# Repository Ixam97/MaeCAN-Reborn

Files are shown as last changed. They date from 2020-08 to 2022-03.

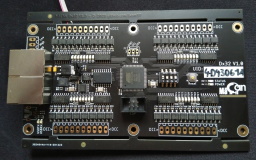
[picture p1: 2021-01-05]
MaeCAN_Dx32/img/Dx32_2_prev.jpg

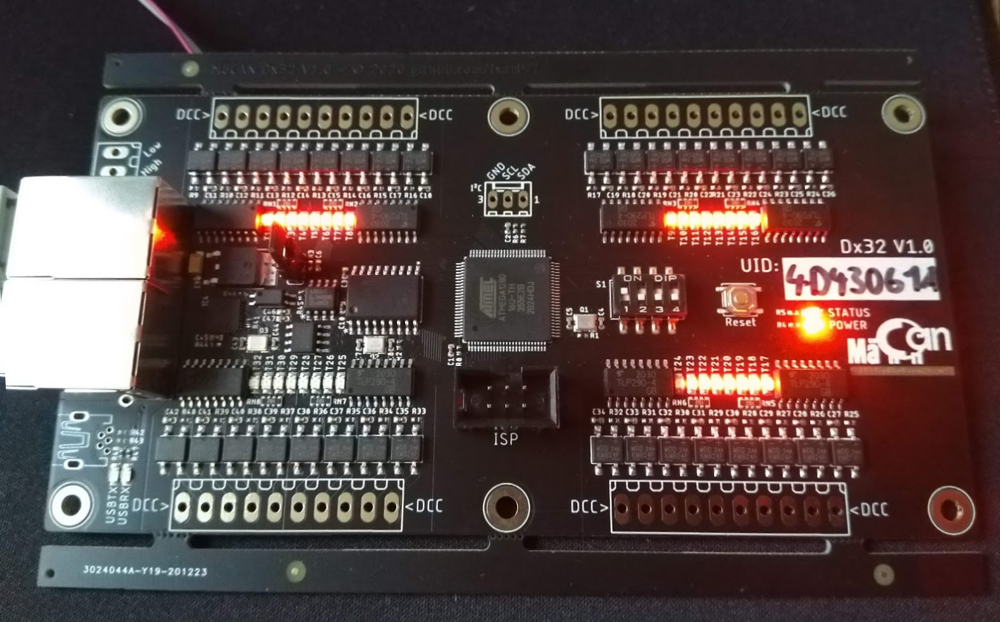
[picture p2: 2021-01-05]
MaeCAN_Dx32/img/Dx32_3.jpg

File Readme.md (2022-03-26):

# <b>MäCAN _Reborn_ </b>

Die zweite Generaton der MäCAN-Komponenten für den [Märklin CAN-Bus][candoku]

- <b>[MäCAN _Bootloader_][bootloader]</b><br>
    
- <b>[MäCAN _MP5x16_][mp5x16]</b><br>
    
    
- <b>[MäCAN _Dx32_][dx32]</b><br>
    
    
## Changelog

### [2022-03-26.1]
#### Hinzugefügt:
 - MP5x8+S: Kombination aus Signal- und Weichendecoder zum testen, kompatibel mit der MP5x16-Platine.
#### Änderungen:
 - MP5+D | Rückmeldefehler behoben, Einstellungen für die Schaltzeit und -verzögerung.
 - MP5x16 | Rückmeldefehler behoben.
 - Bootloader | Unterstützt nun 16-Bit Page-Addresse (Rückwärtskomatibel mit alten Updatern).
 - Bootloader | Nach einem fehlerhaften oder abgebrochenen Update wird der Programmspeicher gelöscht. Das Gerät verbleibt im Booloader, bis ein Update erfolgreich abgeschlossen wurde.
 - Allgemein | Der CAN-Ringpuffer blockiert nicht mehr, wenn er voll läuft.

### [2021-09-14.1]
#### Hinzugefügt:
- Allgemein | Source und Binarys für den maecan-updater für SRSEII und Windows.
- Bootloader | Unterstützung für NScale Grundmodule.
- MP5+D | Abwandlung des MP5x16 für die alternative Nutzung einiger Ports.
#### Änderungen:
- MP5x16 | Korrekte Abhandlung von Config-Kanal-Abfragen durch ein Userinterface.
- Bootloader | UID-Vergleich korrigiert.
### [2021-03-13.2]
#### Hinzugefügt:
- Allgemein | Fehlermeldung hinzugefügt, falls MCAN mit einem nicht unterstützten Controller verwendet wird.

### [2021-03-13.1]
#### Änderungen:
- Allgemein | Die Dokumentation in mcan.h wurde umfangreich erweitert.
- Allgemein | Die Berechnung des Hash wird durch mcan_init() übernommen. Die vorgefertigten send-Funktionen benötigen keine UID und keinen Hash mehr als Parameter. Dx32 und MP5x16 wurden entsprechend angepasst.
- Allgemein compareUID() ist jetzt Teil von MCAN.

### [2021-03-12.1]
#### Änderungen:
- Allgemein | MCAN beinhaltet nun mcp2515_basic und wurde aufgeräumt, um die Nutzung zu vereinfachen. Eine nutzung in Arduino-Sketches ist möglich.

#### Hinzugefügt:
- Dx32 | Version 1.0, Konfiguration und EEPROM-Nutzung wurde vollständig integriert. 
- Dx32 | Der DIP-Schalter stellt folgende Funktionen bereit: 1: Bootloader-Modus (noch nicht im Bootloader integriert), 2: New Line bei SLCAN zum Debugging, 3: Silent-Mode reagiert nicht auf Ping-Anfragen

### [2021-01-27.1]
#### Hinzugefügt:
- Allgemein | In mcp2515_basic ist nun SLCAN integriert. Ist das Symbol "SLCAN" definiert wird die serielle Schnittstelle als CAN-Interface genutzt. Standard sind 500000 Baud. Hierfür wurde die Interruptbehandlung in mcp2515_basic integriert. Nach `init_mcp2515()` kann mit `readCanFrame()` ausgewertet werden. SLCAN und der physische CAN werden gleichwertig behandelt. Im selben Zuge wurde für CAN-Frames ein Ring-Buffer implementiert. SLCAN ist auch im Bootloader verfügbar.

#### Änderungen:
- MP5x16 | Die Ansteuerung der Status-LED wurde an Dx32 angeglichen.

### [2021-01-25.1]
#### Hinzugefügt:
- Allgemein | Neue Funktion "sendStatus" in der mcan-Bibliothek zum senden von Statuskanalwerten.
- Dx32 | Konfigurationskanal-Werte können abgefragt werden.

### [2021-01-24.1]
#### Änderungen:
- Allgemein | Ein Fehler in der Übertragung von Konfigurationskanälen in der mcan.c wurde behoben.
- Dx32 | Basisfunktionalität wurde hergestellt (Belegterkennung mit Timeout und Gleisspannungserkennung).

### [2021-01-05.1]
#### Änderungen:
- Allgemein | Die Firmware aller Koponenten sowie des Bootloaders wurden in einer Atmel Studio-Solution zusammen geführt, um auf gemeinsame Dateien zugreifen zu können.
- Allgemein | Vereinheitlichung von Ordner- und Dateinamen ohne Umlaute.
- Allgemein | Nicht benötigte defines in mcan.h entfernt und für den ATmega1280 hinzugefügt.
- MP5x16 | Die Heartbeat-LED hat einen Fade-Effekt erhalten.
- Bootloader | Unterstützung für den Dx32 mit ATmega1280.
- Dx32 | Leitungsbenennung für zwei Rückmelde-LEDs an die Portbenennung angepasst.

#### Hinzugefügt:
- Dx32 | Erste Testsoftware mit einem Lauflicht und Helligkeitssteuerung für die Rückmelde-LEDs.

### [2020-12-26.2]
#### Änderungen:
- Bootloader + MP5x16 | Anpassung an die Compiler-Flags für die CPU-Frequenz, da Delays nicht richtig funktioniert haben.
- MP5x16 | Kleinere Änderungen, mit denen bisherige Compiler-Warnungen behandelt wurden.

### [2020-12-26.1]
#### Änderungen:
- Dx32 | Fehlerhafte Anbindung der externen Taktquelle für die USB-Schnittstelle korrigiert (Hardware V1.1).
- Bootloader | Makefile hinzugefügt, mit der der Bootloader Außerhalb von Atmel Studio für eines oder alle Boards kompilliert werden kann (Software V1.2).
- Bootloader | main.c durch maecan-bootloader.c ersetzt.

#### Hinzugefügt:
- Bootloader | Vorkompillierte Hex-Dateien für Busankoppler und MP5x16 hinzugefügt.

### [2020-12-22.1]
#### Änderungen:
- MP5x16 | Möglichkeit einer einstellbaren ID über den DIP-Schalter für eine einfachere Adressierung.

#### Hinzugefügt
- Dx32 | Erster Upload der Hardware.

### [2020-08-27.2]
#### Änderungen:
- Readme-Dateien angepasst

### [2020-08-27.1]
#### Hinzugefügt:
- MP5x16 | Erster Upload
- Bootloader |  Erster Upload

[candoku]: https://www.maerklin.de/fileadmin/media/service/software-updates/cs2CAN-Protokoll-2_0.pdf
[bootloader]: Bootloader
[mp5x16]: MäCAN_MP5x16
[dx32]: MäCAN_Dx32

[//]: # (Orange: #FE7D37, Blau: #007EC6)

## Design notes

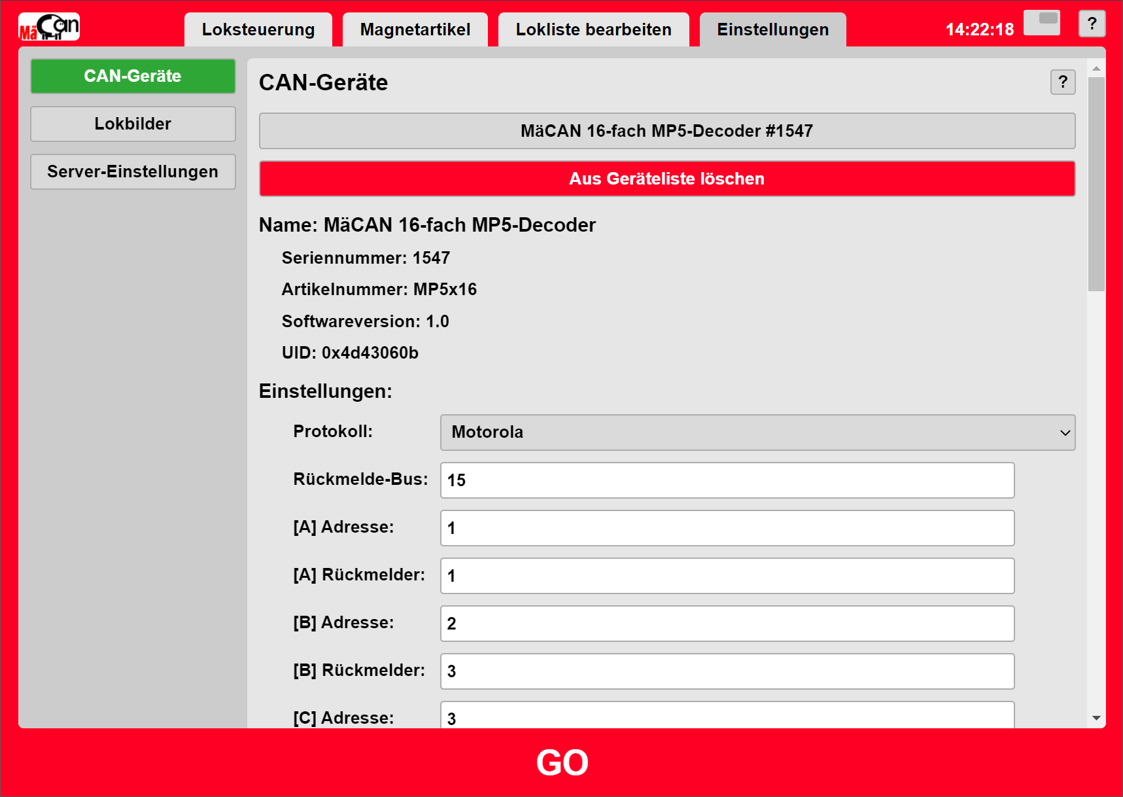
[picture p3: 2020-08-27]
MaeCAN_MP5x16/img/MP5x16_ui_1.png

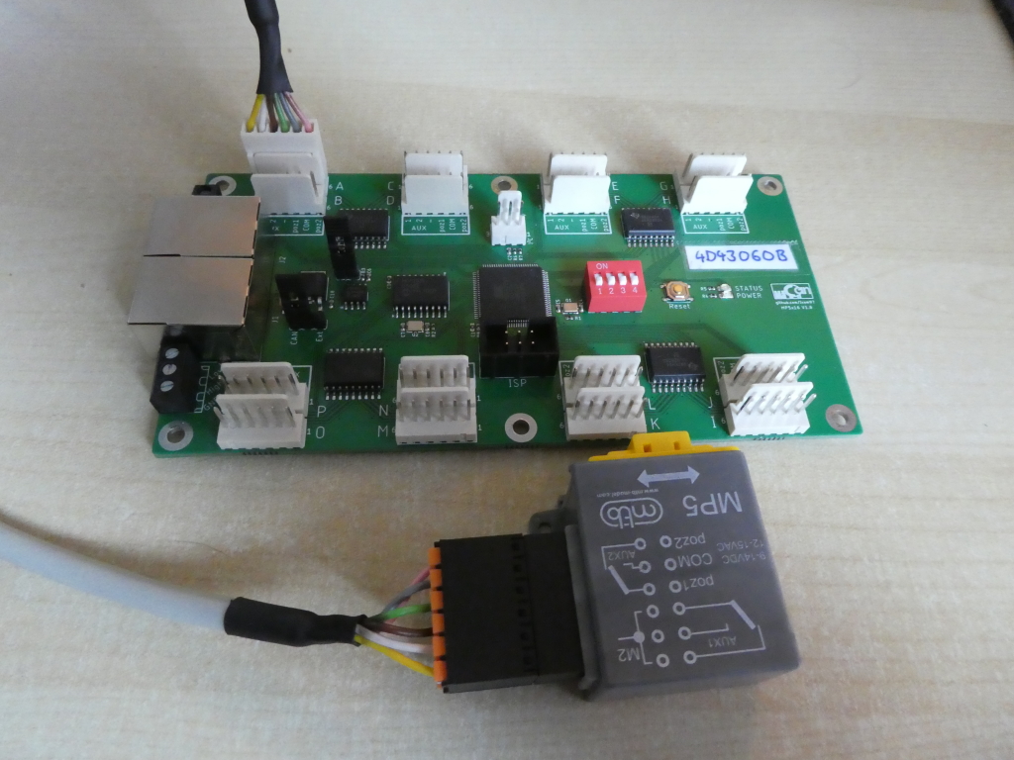
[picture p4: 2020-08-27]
MaeCAN_MP5x16/img/MP5x16_2.jpg

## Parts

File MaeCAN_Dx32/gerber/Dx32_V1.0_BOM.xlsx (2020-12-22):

Qty | Designator | Footprint | Comment | LCSC Part #
8 | RN1, RN2, RN3, RN4, RN5, RN6, RN7, RN8 | 0603_x4 | 1k | C20197
1 | C9 | CASE-A_3216 | 10u | C7171
39 | C1, C2, C3, C6, C10, C11, C12, C13, C14, C15, C16, C17, C18, C19, C20, C21, C22, C23, C24, C25, C26, C27, C28, C29, C30, C31, C32, C33, C34, C35, C36, C37, C38, C39, C40, C41, C42, C46, C47 | C0402 | 100n | C1525
5 | R6, R7, R8, R44, R45 | R0402 | 10k | C25744
1 | R3 | R0402 | 120 | C25079
3 | Q1, Q2, Q3 | 3.2X2.5_KX-7 | 16MHZ | C13738
3 | R1, R2, R41 | R0402 | 1M | C26083
4 | R4, R5, R47, R48 | R0402 | 1k | C11702
1 | C45 | C0402 | 1u | C52923
2 | R42, R43 | R0402 | 22 | C25092
6 | C4, C5, C7, C8, C43, C44 | C0402 | 22p | C1555
32 | R9, R10, R11, R12, R13, R14, R15, R16, R17, R18, R19, R20, R21, R22, R23, R24, R25, R26, R27, R28, R29, R30, R31, R32, R33, R34, R35, R36, R37, R38, R39, R40 | R0402 | 33 | C25105
1 | R46 | R0402 | 330 | C25104
1 | IC5 | SOIC-8_3.9x4.9x1.27P | ADUM1201ARZ-RL7 | C9669
1 | IC4 | QFN-32_EP_5.0x5.0x0.5P | ATMEGA16U2 | C17317
1 | IC1 | QFP-100_14.0x14.0x0.5P | ATMEGA2560 | C22460
1 | RESET | SMD-SW-4 | TS-1187A-B-A-B | C318884
32 | B1, B2, B3, B4, B5, B6, B7, B8, B9, B10, B11, B12, B13, B14, B15, B16, B17, B18, B19, B20, B21, B22, B23, B24, B25, B26, B27, B28, B29, B30, B31, B32 | MBF_3.8x4.7x2.5P | KMB24F | C113927
1 | IC8 | TO-252-2 | L78M05 | C58069
1 | IC3 | SOIC-18 | MCP2515-I/SO | C12368
1 | IC2 | SOIC-8 | TJA1050 | C6952
1 | S1 | SW-SMD-8_6.2x11.1x2.54P | DMR-04-V-T/R | C225009
1 | OK9 | SOP-4_2.7x4.4x1.27P | TLP290 | C73839
8 | OK1, OK2, OK3, OK4, OK5, OK6, OK7, OK8 | SOIC-16_4.4x10.3x1.27P | TLP290-4 | C39031
3 | STATUS, USBRX, USBTX | LED_0805 | yellow | C2296
33 | POWER, T1, T2, T3, T4, T5, T6, T7, T8, T9, T10, T11, T12, T13, T14, T15, T16, T17, T18, T19, T20, T21, T22, T23, T24, T25, T26, T27, T28, T29, T30, T31, T32 | LED_0805 | red | C84256

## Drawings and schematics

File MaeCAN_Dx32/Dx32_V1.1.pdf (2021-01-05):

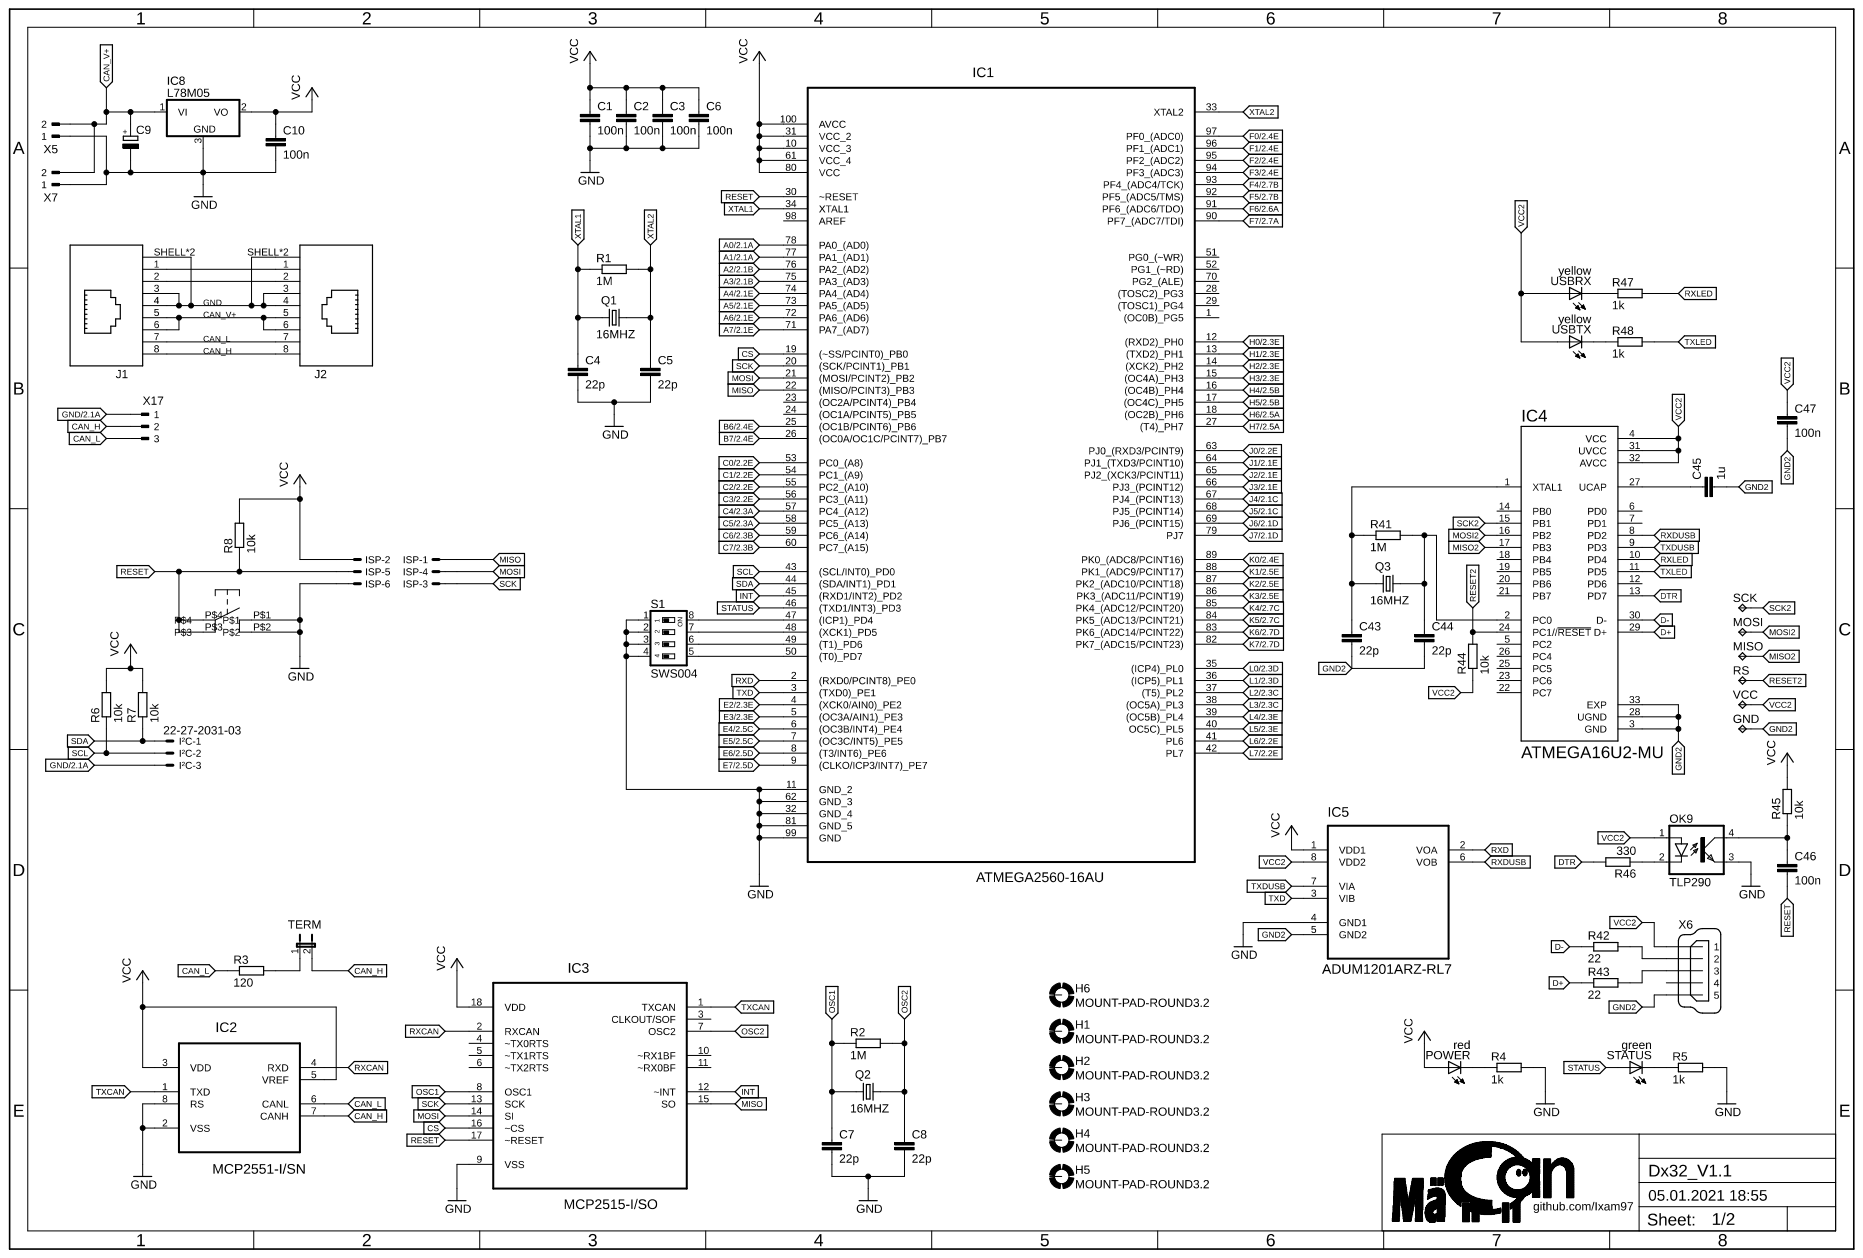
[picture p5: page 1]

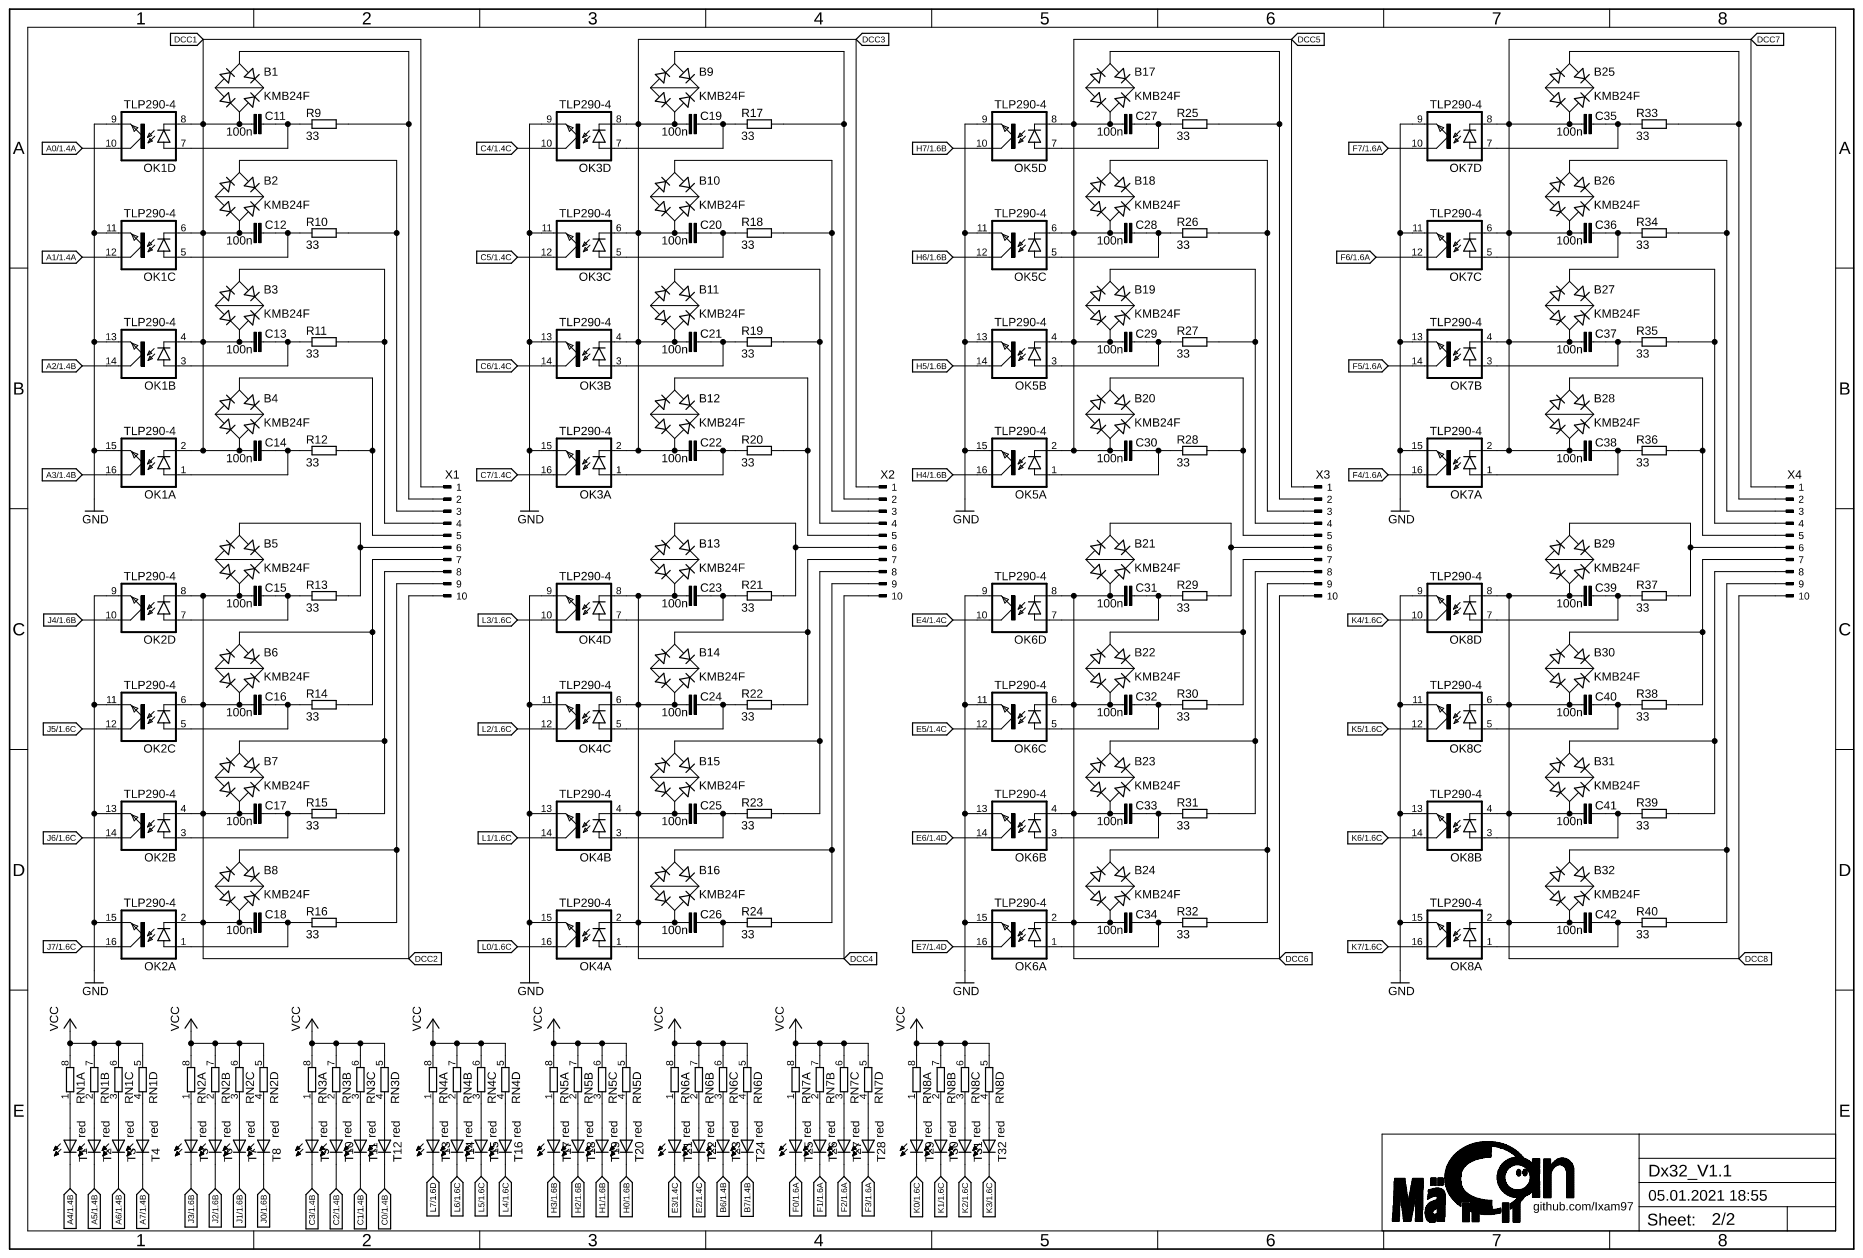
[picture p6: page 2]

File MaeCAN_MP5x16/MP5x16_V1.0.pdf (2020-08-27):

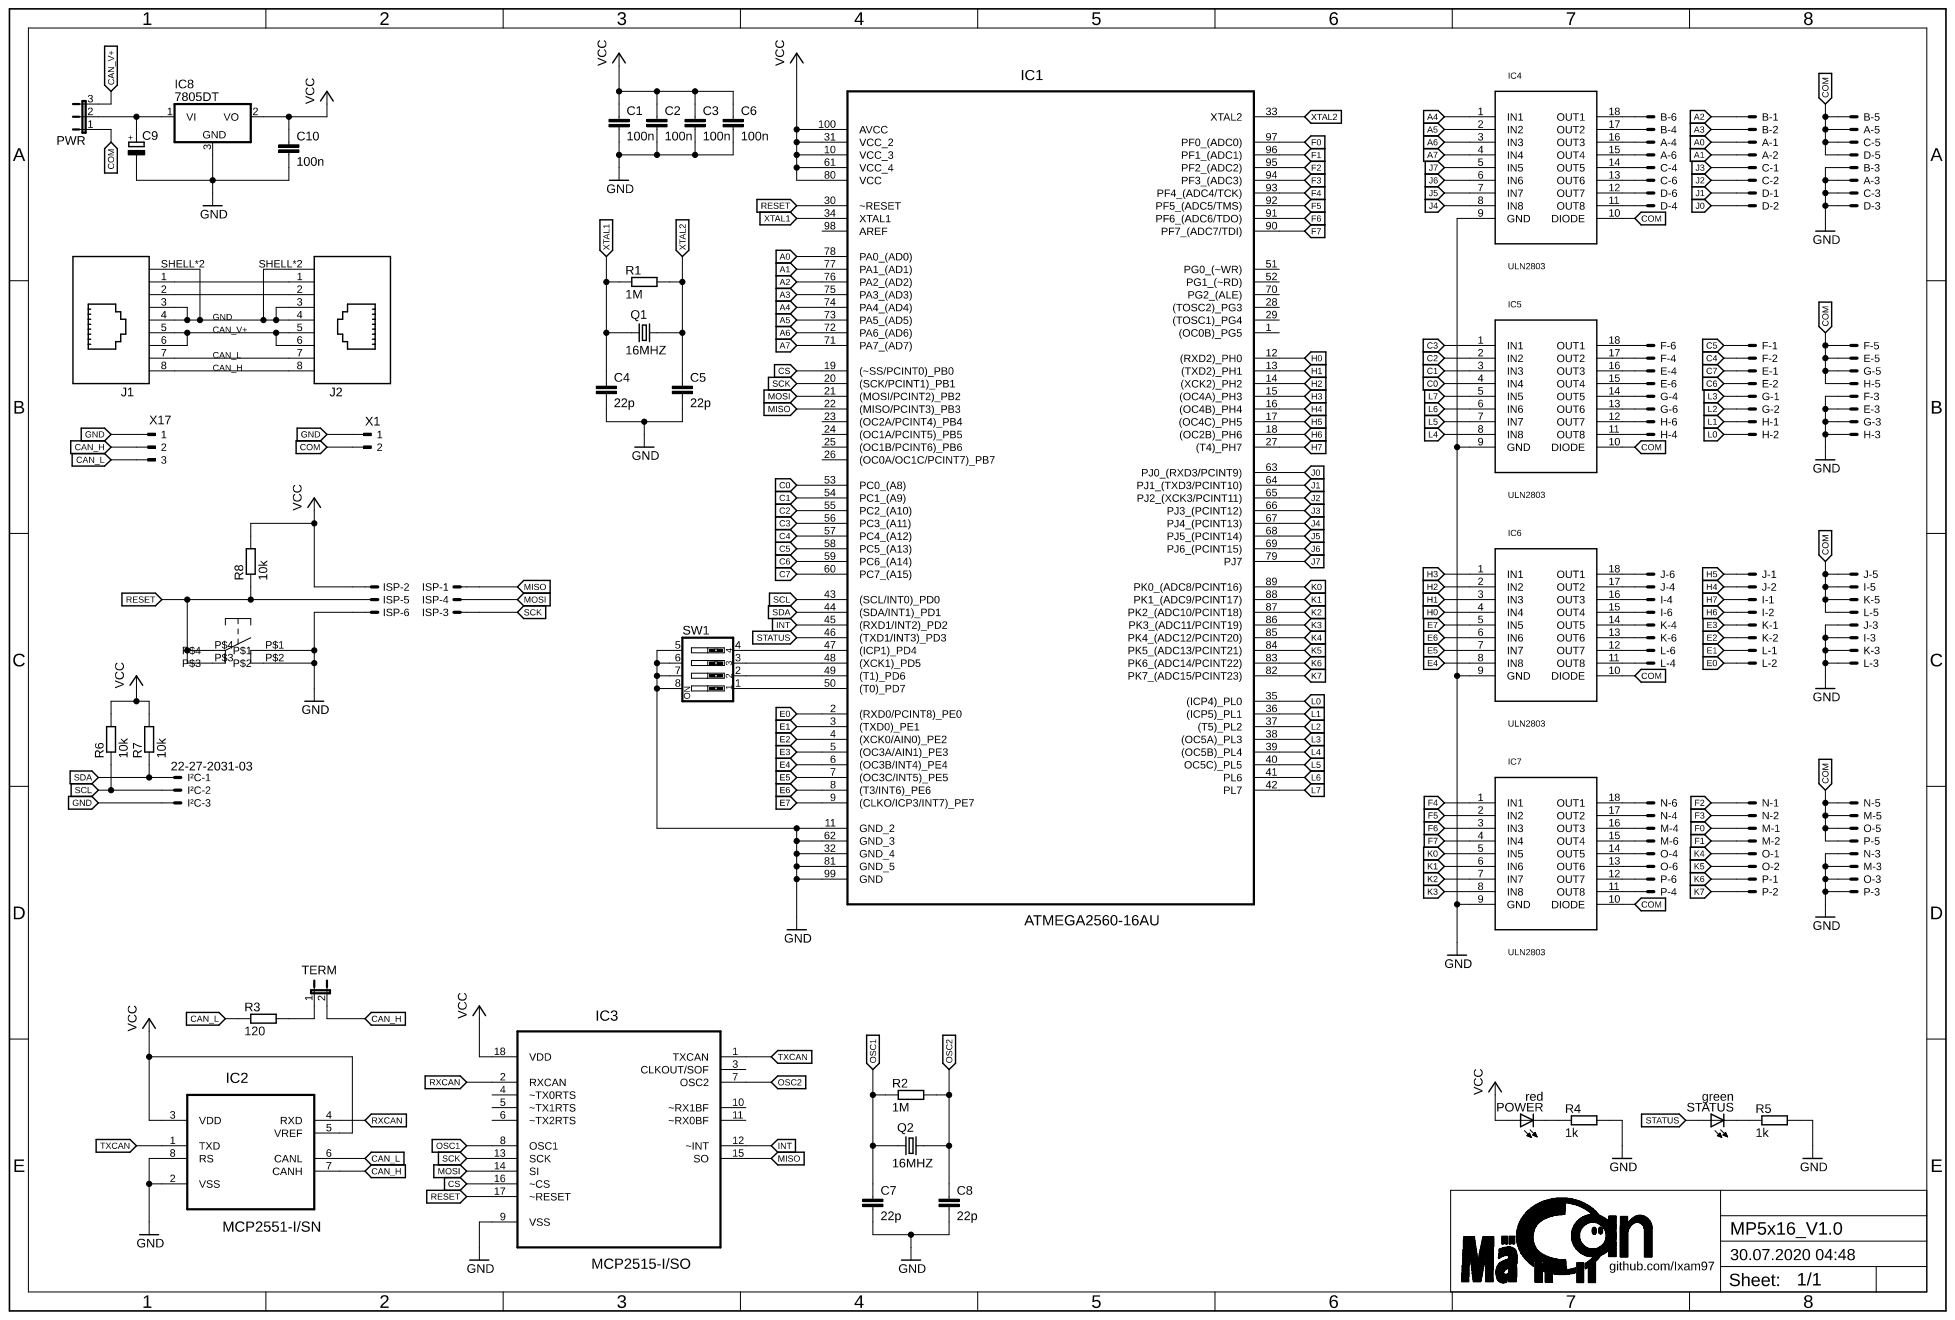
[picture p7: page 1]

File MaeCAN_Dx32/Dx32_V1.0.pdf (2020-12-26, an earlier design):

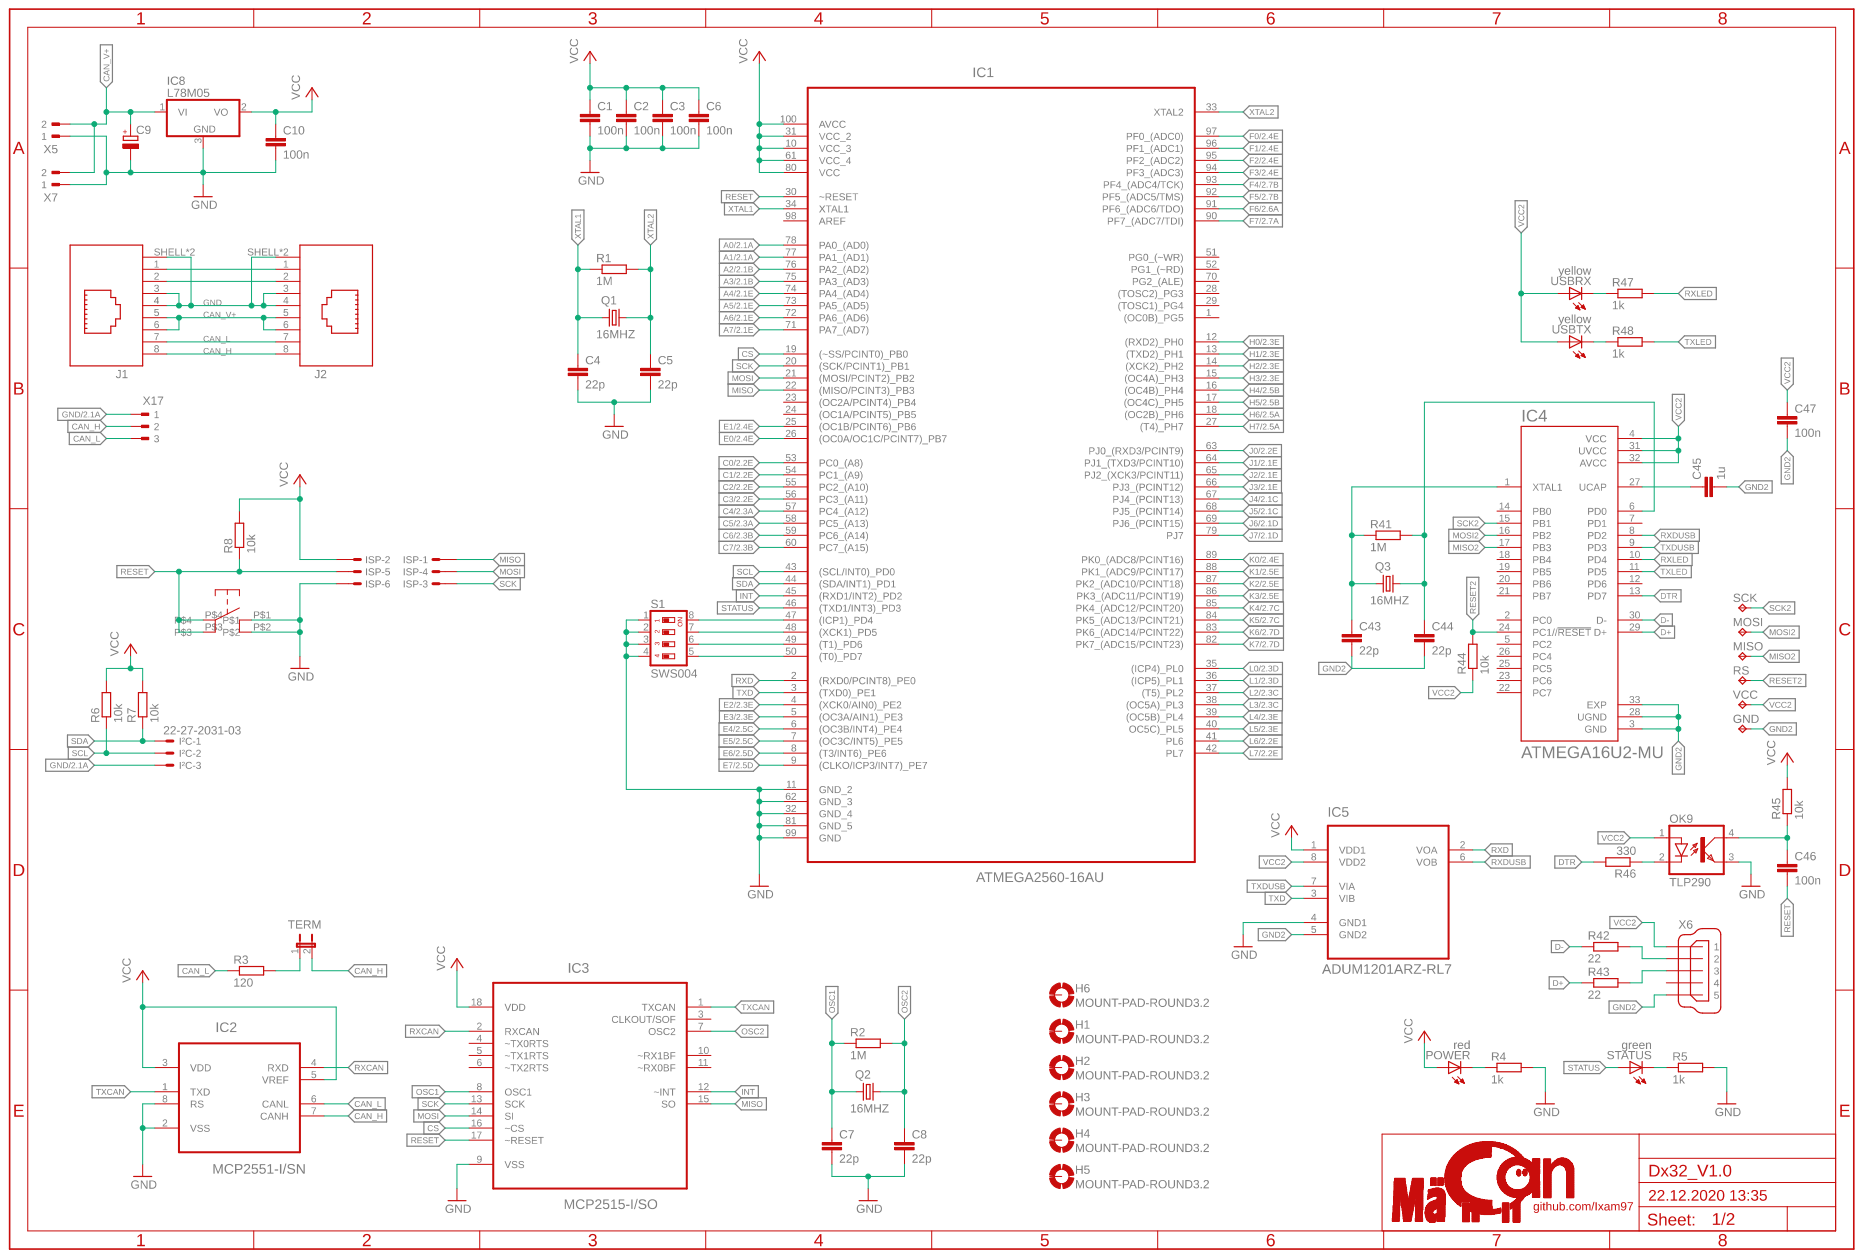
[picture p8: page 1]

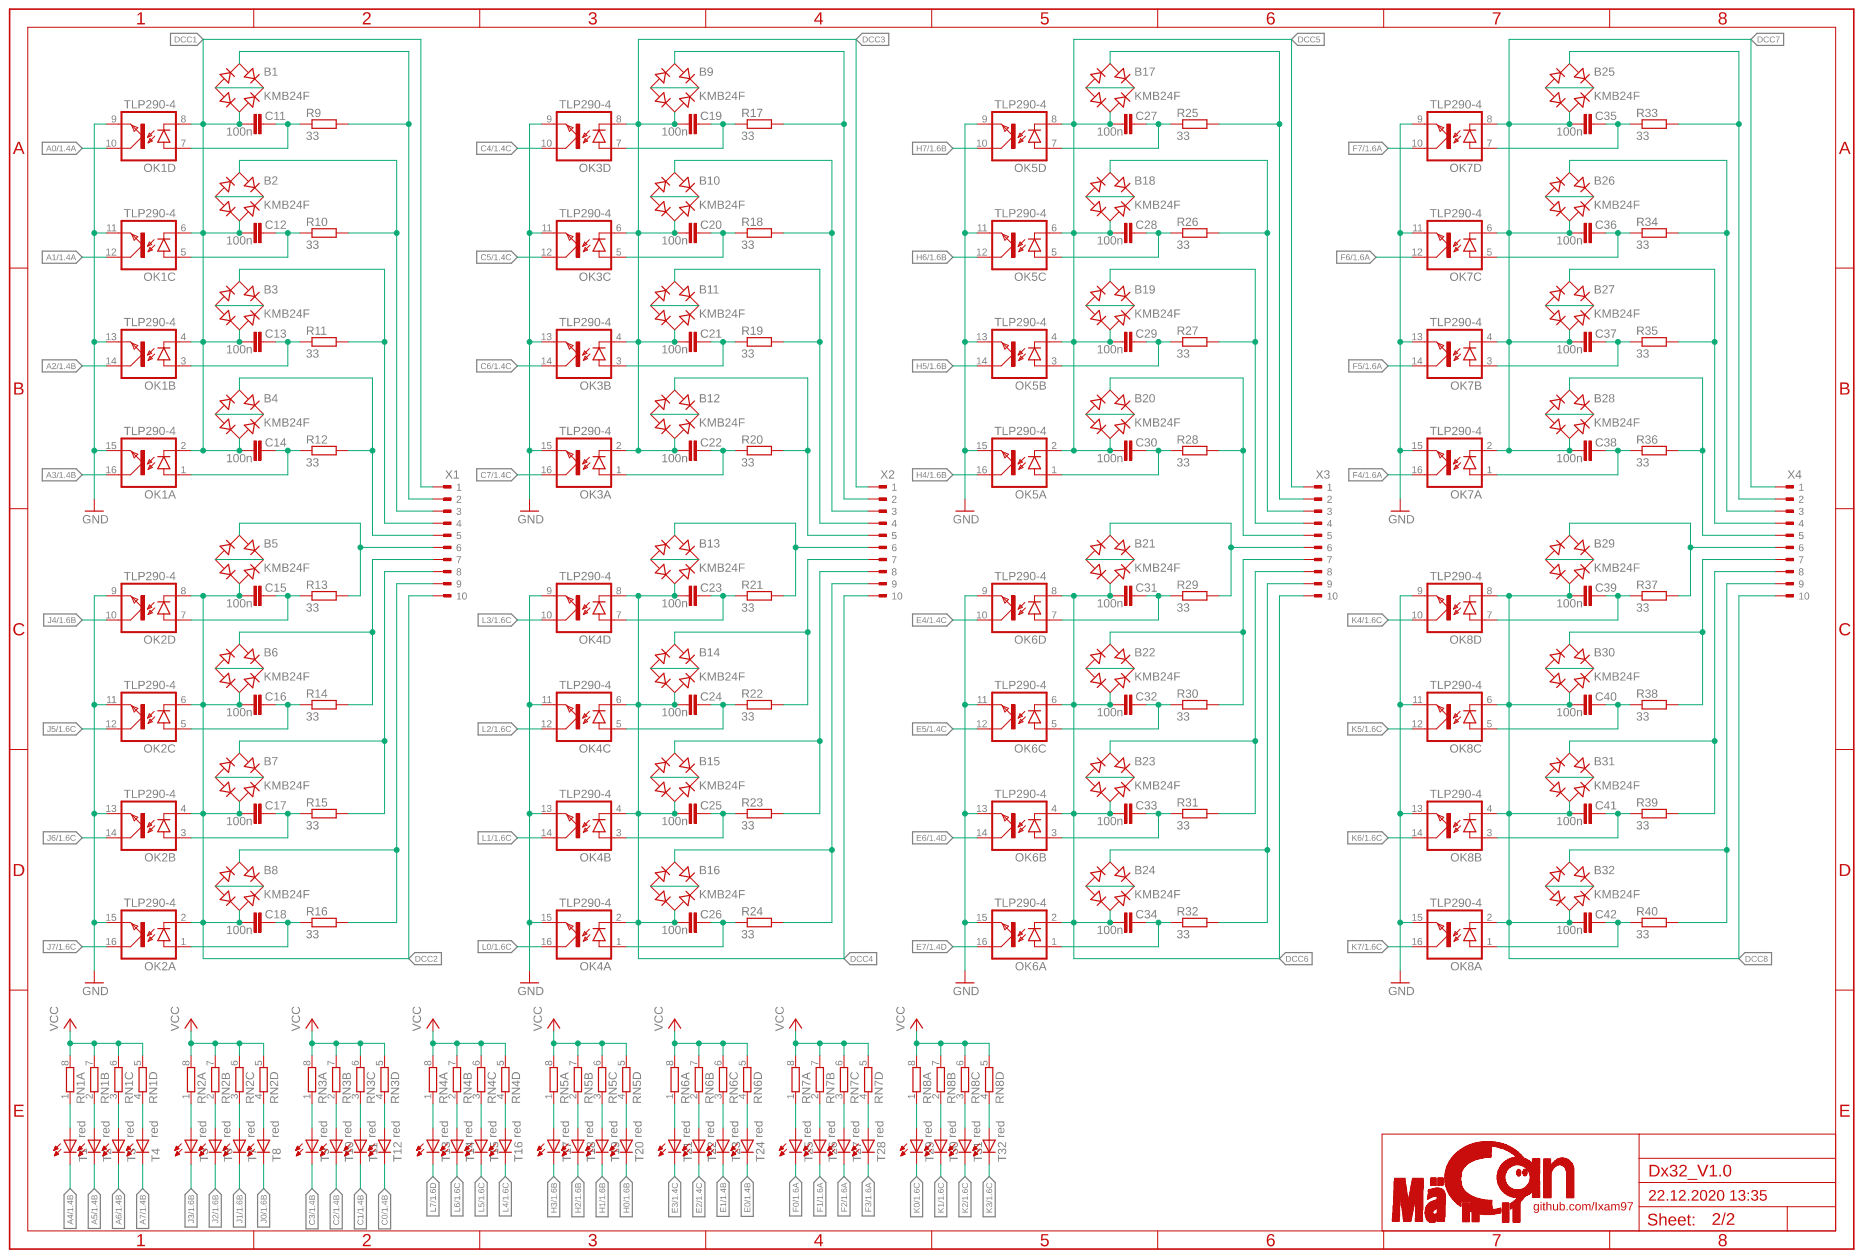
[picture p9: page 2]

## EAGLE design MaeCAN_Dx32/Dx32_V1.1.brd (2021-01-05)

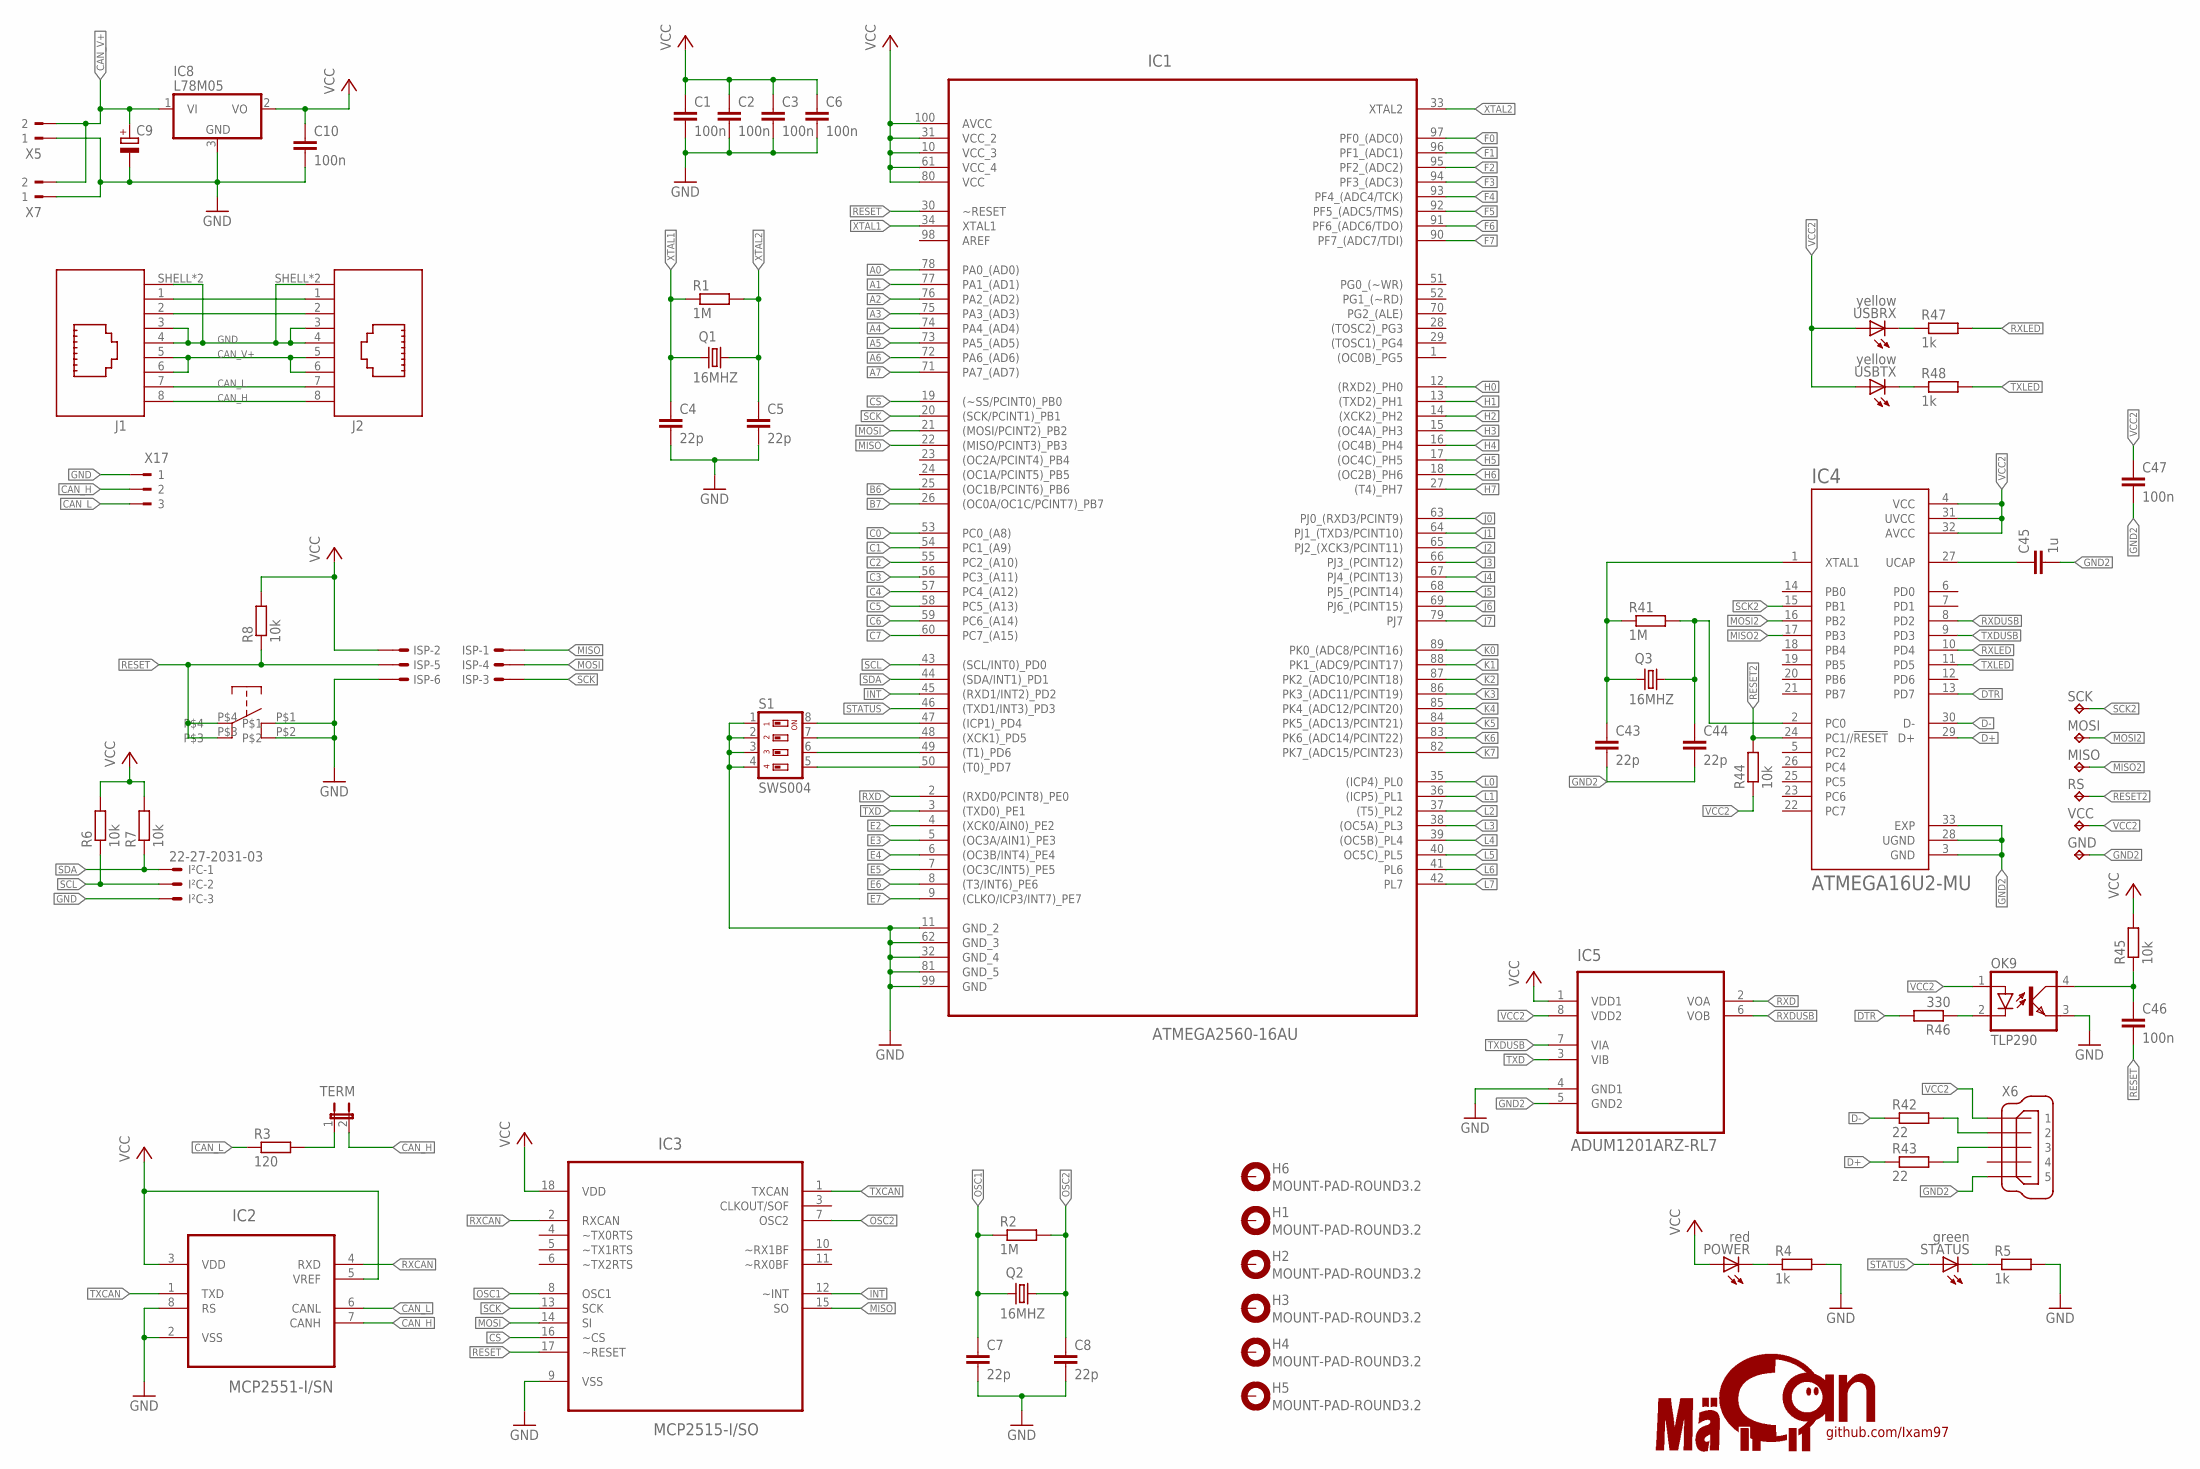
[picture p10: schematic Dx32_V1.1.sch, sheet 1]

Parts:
C1, C2, C3, C6, C10, C46, C47: 100n; C0402
C4, C5, C7, C8, C43, C44: 22p; C0402
C9: CPOL-EUCT3216; CT3216
C45: 1u; C0402
GND: TPB1,27; B1,27
H1, H2, H3, H4, H5, H6: MOUNT-PAD-ROUND3.2; 3,2-PAD
IC1: ATMEGA2560-16AU; QFP50P1600X1600X120-100N
IC2: MCP2551-I/SN; SOIC127P600X175-8N
IC3: MCP2515-I/SO; SOIC127P1034X264-18N
IC4: ATMEGA16U2-MU; QFN50P500X500X100-33N
IC5: ADUM1201ARZ-RL7; SOIC127P600X175-8N
IC8: L78M05; TO252; JLCPCB-PART C58069
ISP: 057-006-1
I²C: 22-27-2031-03; 6410-03
J1, J2: 615008140421
MISO: TPB1,27; B1,27
MOSI: TPB1,27; B1,27
OK9: TLP290; MINI-FLAT-4
POWER: red; CHIP-LED0805
Q1, Q2, Q3: 16MHZ; 3.2X2.5_KX-7
R1, R2, R41: 1M; R0402
R3: 120; R0402
R4, R5, R47, R48: 1k; R0402
R6, R7, R8, R44, R45: 10k; R0402
R42, R43: 22; R0402
R46: 330; R0402
RS: TPB1,27; B1,27
S1: SWS004; SMS-004
SCK: TPB1,27; B1,27
STATUS: green; CHIP-LED0805
TERM: JP1E; JP1
U$15: BUTTON_JLC; BUTTON
USBRX: yellow; CHIP-LED0805
USBTX: yellow; CHIP-LED0805
VCC: TPB1,27; B1,27
X5, X7: 180-2
X6: MINI-USB_SHIELD5P2-32005-601; 32005-601
X17: 180-3

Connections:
A0: IC1.78 (PA0_(AD0)); also elsewhere on the board
A1: IC1.77 (PA1_(AD1)); also elsewhere on the board
A2: IC1.76 (PA2_(AD2)); also elsewhere on the board
A3: IC1.75 (PA3_(AD3)); also elsewhere on the board
A4: IC1.74 (PA4_(AD4)); also elsewhere on the board
A5: IC1.73 (PA5_(AD5)); also elsewhere on the board
A6: IC1.72 (PA6_(AD6)); also elsewhere on the board
A7: IC1.71 (PA7_(AD7)); also elsewhere on the board
B6: IC1.25 ((OC1B/PCINT6)_PB6); also elsewhere on the board
B7: IC1.26 ((OC0A/OC1C/PCINT7)_PB7); also elsewhere on the board
C0: IC1.53 (PC0_(A8)); also elsewhere on the board
C1: IC1.54 (PC1_(A9)); also elsewhere on the board
C2: IC1.55 (PC2_(A10)); also elsewhere on the board
C3: IC1.56 (PC3_(A11)); also elsewhere on the board
C4: IC1.57 (PC4_(A12)); also elsewhere on the board
C5: IC1.58 (PC5_(A13)); also elsewhere on the board
C6: IC1.59 (PC6_(A14)); also elsewhere on the board
C7: IC1.60 (PC7_(A15)); also elsewhere on the board
CAN_H: IC2.7 (CANH), J1.8, J2.8, TERM.2, X17.2
CAN_L: IC2.6 (CANL), J1.7, J2.7, R3.1, X17.3
CAN_V+: C9.+, IC8.1 (VI), J1.5, J1.6, J2.5, J2.6, X5.2, X7.2
CS: IC1.19 ((~SS/PCINT0)_PB0), IC3.16 (~CS)
D+: IC4.29 (D+), R43.1
D-: IC4.30 (D-), R42.1
DTR: IC4.13 (PD7), R46.2
E2: IC1.4 ((XCK0/AIN0)_PE2); also elsewhere on the board
E3: IC1.5 ((OC3A/AIN1)_PE3); also elsewhere on the board
E4: IC1.6 ((OC3B/INT4)_PE4); also elsewhere on the board
E5: IC1.7 ((OC3C/INT5)_PE5); also elsewhere on the board
E6: IC1.8 ((T3/INT6)_PE6); also elsewhere on the board
E7: IC1.9 ((CLKO/ICP3/INT7)_PE7); also elsewhere on the board
F0: IC1.97 (PF0_(ADC0)); also elsewhere on the board
F1: IC1.96 (PF1_(ADC1)); also elsewhere on the board
F2: IC1.95 (PF2_(ADC2)); also elsewhere on the board
F3: IC1.94 (PF3_(ADC3)); also elsewhere on the board
F4: IC1.93 (PF4_(ADC4/TCK)); also elsewhere on the board
F5: IC1.92 (PF5_(ADC5/TMS)); also elsewhere on the board
F6: IC1.91 (PF6_(ADC6/TDO)); also elsewhere on the board
F7: IC1.90 (PF7_(ADC7/TDI)); also elsewhere on the board
GND: C1.2, C2.2, C3.2, C4.2, C5.2, C6.2, C7.2, C8.2, C9.-, C10.2, IC1.11 (GND_2), IC1.32 (GND_4), IC1.62 (GND_3), IC1.81 (GND_5), IC1.99 (GND), IC2.2 (VSS), IC2.8 (RS), IC3.9 (VSS), IC5.4 (GND1), IC8.3 (GND), ISP.6, I²C.3, J1.3, J1.4, J1.SHELL (SHIELD), J1.SHELL1 (SHIELD), J2.3, J2.4, J2.SHELL (SHIELD), J2.SHELL1 (SHIELD), OK9.3 (EMIT), R4.2, R5.2, S1.1, S1.2, S1.3, S1.4, U$15.P$1, U$15.P$2, X5.1, X7.1, X17.1; also elsewhere on the board
GND2: C43.2, C44.2, C45.2, C47.2, GND.TP, IC4.3 (GND), IC4.28 (UGND), IC4.33 (EXP), IC5.5 (GND2), X6.5
H0: IC1.12 ((RXD2)_PH0); also elsewhere on the board
H1: IC1.13 ((TXD2)_PH1); also elsewhere on the board
H2: IC1.14 ((XCK2)_PH2); also elsewhere on the board
H3: IC1.15 ((OC4A)_PH3); also elsewhere on the board
H4: IC1.16 ((OC4B)_PH4); also elsewhere on the board
H5: IC1.17 ((OC4C)_PH5); also elsewhere on the board
H6: IC1.18 ((OC2B)_PH6); also elsewhere on the board
H7: IC1.27 ((T4)_PH7); also elsewhere on the board
INT: IC1.45 ((RXD1/INT2)_PD2), IC3.12 (~INT)
J0: IC1.63 (PJ0_(RXD3/PCINT9)); also elsewhere on the board
J1: IC1.64 (PJ1_(TXD3/PCINT10)); also elsewhere on the board
J2: IC1.65 (PJ2_(XCK3/PCINT11)); also elsewhere on the board
J3: IC1.66 (PJ3_(PCINT12)); also elsewhere on the board
J4: IC1.67 (PJ4_(PCINT13)); also elsewhere on the board
J5: IC1.68 (PJ5_(PCINT14)); also elsewhere on the board
J6: IC1.69 (PJ6_(PCINT15)); also elsewhere on the board
J7: IC1.79 (PJ7); also elsewhere on the board
K0: IC1.89 (PK0_(ADC8/PCINT16)); also elsewhere on the board
K1: IC1.88 (PK1_(ADC9/PCINT17)); also elsewhere on the board
K2: IC1.87 (PK2_(ADC10/PCINT18)); also elsewhere on the board
K3: IC1.86 (PK3_(ADC11/PCINT19)); also elsewhere on the board
K4: IC1.85 (PK4_(ADC12/PCINT20)); also elsewhere on the board
K5: IC1.84 (PK5_(ADC13/PCINT21)); also elsewhere on the board
K6: IC1.83 (PK6_(ADC14/PCINT22)); also elsewhere on the board
K7: IC1.82 (PK7_(ADC15/PCINT23)); also elsewhere on the board
L0: IC1.35 ((ICP4)_PL0); also elsewhere on the board
L1: IC1.36 ((ICP5)_PL1); also elsewhere on the board
L2: IC1.37 ((T5)_PL2); also elsewhere on the board
L3: IC1.38 ((OC5A)_PL3); also elsewhere on the board
L4: IC1.39 ((OC5B)_PL4); also elsewhere on the board
L5: IC1.40 (OC5C)_PL5); also elsewhere on the board
L6: IC1.41 (PL6); also elsewhere on the board
L7: IC1.42 (PL7); also elsewhere on the board
MISO: IC1.22 ((MISO/PCINT3)_PB3), IC3.15 (SO), ISP.1
MISO2: IC4.17 (PB3), MISO.TP
MOSI: IC1.21 ((MOSI/PCINT2)_PB2), IC3.14 (SI), ISP.4
MOSI2: IC4.16 (PB2), MOSI.TP
unnamed: C46.1, OK9.4 (COL), R45.1
unnamed: IC1.47 ((ICP1)_PD4), S1.8
unnamed: IC1.48 ((XCK1)_PD5), S1.7
unnamed: IC1.49 ((T1)_PD6), S1.6
unnamed: IC1.50 ((T0)_PD7), S1.5
unnamed: J1.1, J2.1
unnamed: OK9.2 (C), R46.1
unnamed: J1.2, J2.2
unnamed: R48.1, USBTX.C
unnamed: R47.1, USBRX.C
unnamed: C45.1, IC4.27 (UCAP)
unnamed: R42.2, X6.2
unnamed: R43.2, X6.3
unnamed: POWER.C, R4.1
unnamed: R3.2, TERM.1
unnamed: R5.1, STATUS.C
OSC1: C7.1, IC3.8 (OSC1), Q2.1, R2.1
OSC2: C8.1, IC3.7 (OSC2), Q2.3 (2), R2.2
OSC3: C43.1, IC4.1 (XTAL1), Q3.1, R41.1
OSC4: C44.1, IC4.2 (PC0), Q3.3 (2), R41.2
RESET: C46.2, IC1.30 (~RESET), IC3.17 (~RESET), ISP.5, R8.1, U$15.P$3, U$15.P$4
RESET2: IC4.24 (PC1//!RESET), R44.2, RS.TP
RXCAN: IC2.4 (RXD), IC3.2 (RXCAN)
RXD: IC1.2 ((RXD0/PCINT8)_PE0), IC5.2 (VOA)
RXDUSB: IC4.8 (PD2), IC5.6 (VOB)
RXLED: IC4.10 (PD4), R47.2
SCK: IC1.20 ((SCK/PCINT1)_PB1), IC3.13 (SCK), ISP.3
SCK2: IC4.15 (PB1), SCK.TP
SCL: IC1.43 ((SCL/INT0)_PD0), I²C.2, R6.1
SDA: IC1.44 ((SDA/INT1)_PD1), I²C.1, R7.1
STATUS: IC1.46 ((TXD1/INT3)_PD3), STATUS.A
TXCAN: IC2.1 (TXD), IC3.1 (TXCAN)
TXD: IC1.3 ((TXD0)_PE1), IC5.3 (VIB)
TXDUSB: IC4.9 (PD3), IC5.7 (VIA)
TXLED: IC4.11 (PD5), R48.2
VCC: C1.1, C2.1, C3.1, C6.1, C10.1, IC1.10 (VCC_3), IC1.31 (VCC_2), IC1.61 (VCC_4), IC1.80 (VCC), IC1.100 (AVCC), IC2.3 (VDD), IC2.5 (VREF), IC3.18 (VDD), IC5.1 (VDD1), IC8.2 (VO), ISP.2, POWER.A, R6.2, R7.2, R8.2, R45.2; also elsewhere on the board
VCC2: C47.1, IC4.4 (VCC), IC4.31 (UVCC), IC4.32 (AVCC), IC5.8 (VDD2), OK9.1 (A), R44.1, USBRX.A, USBTX.A, VCC.TP, X6.1
XTAL1: C4.1, IC1.34 (XTAL1), Q1.1, R1.1
XTAL2: C5.1, IC1.33 (XTAL2), Q1.3 (2), R1.2

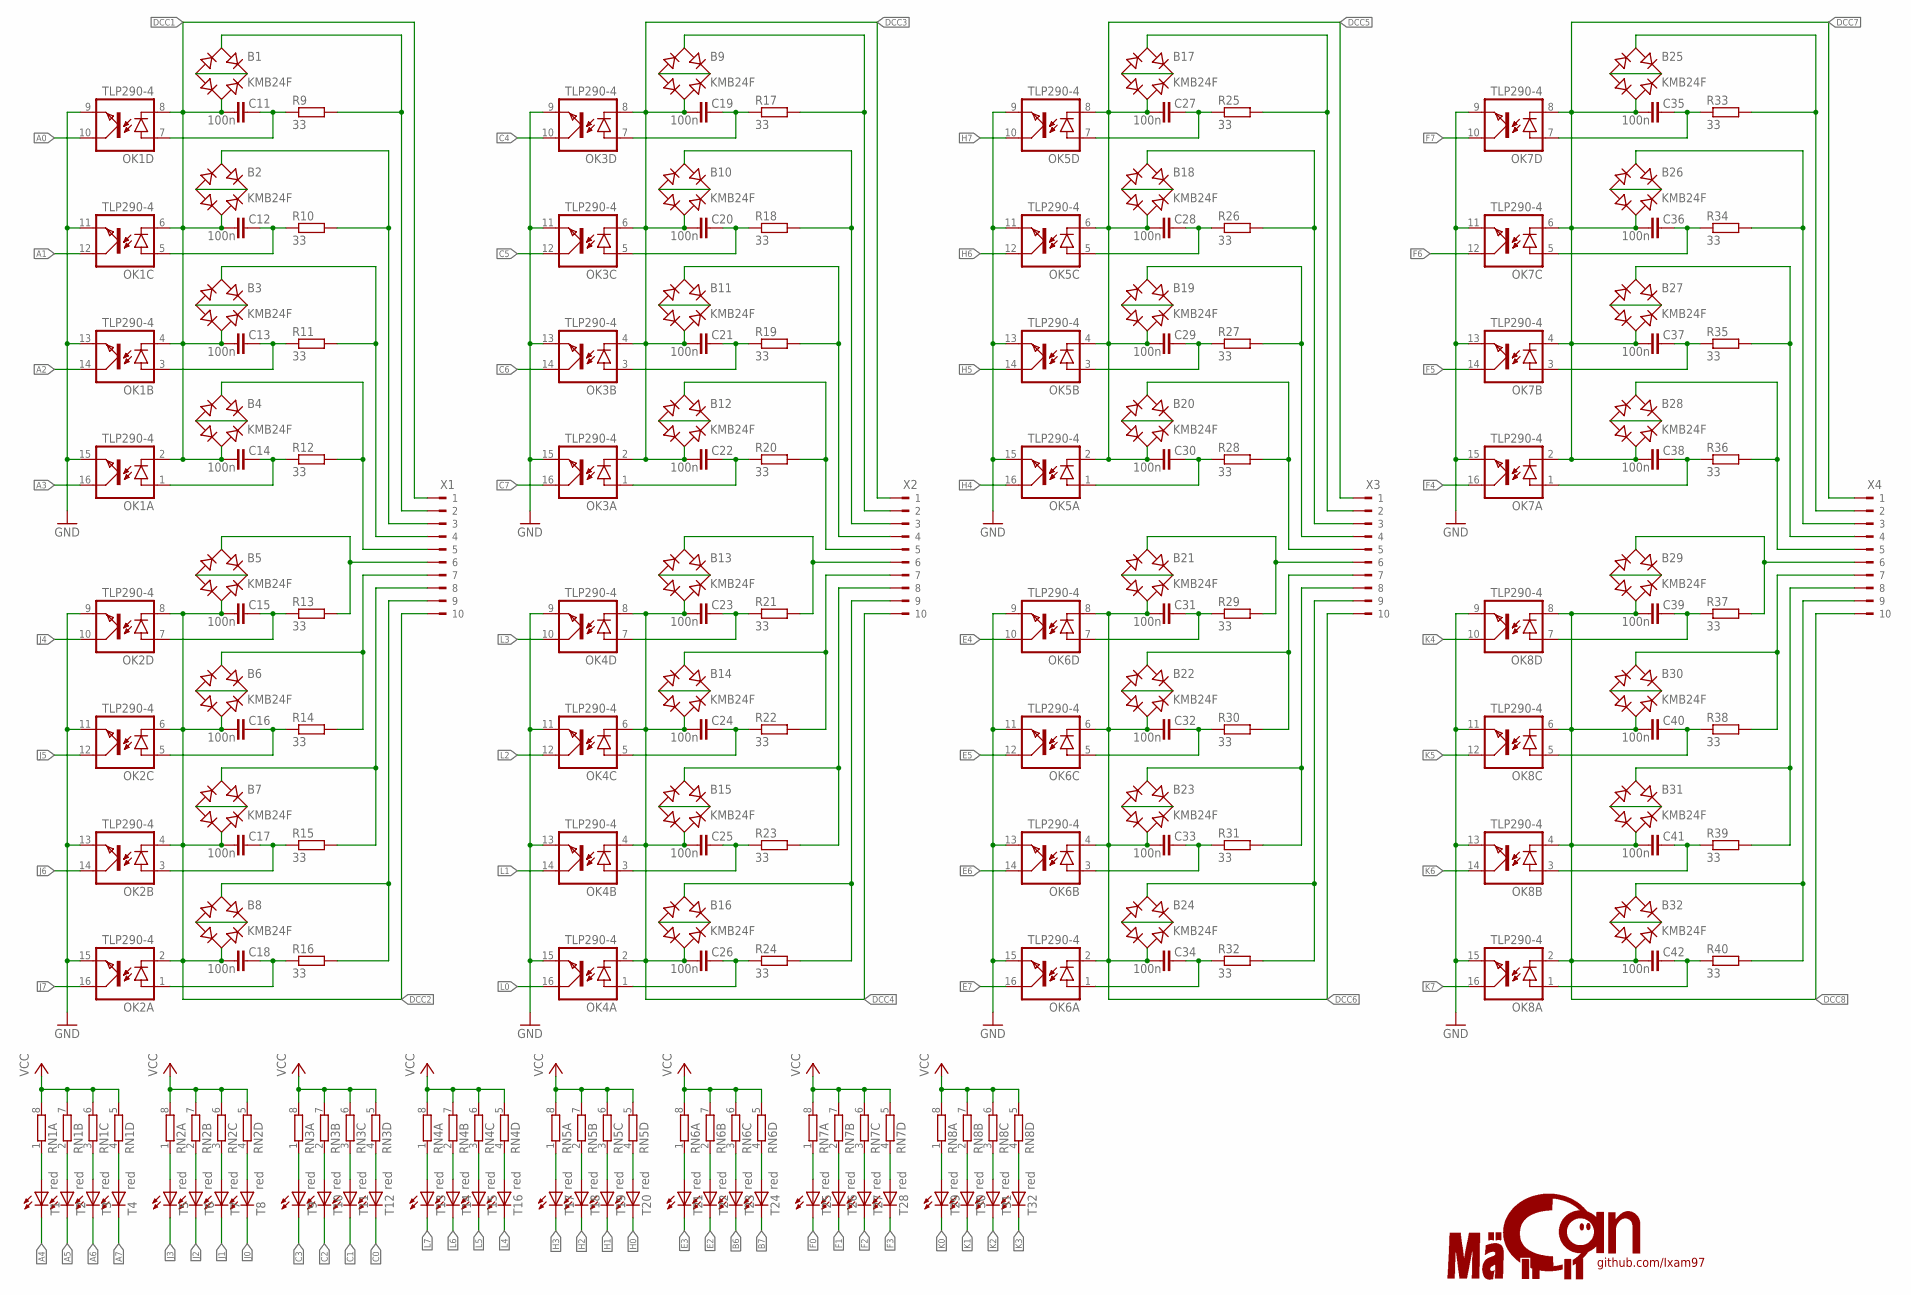
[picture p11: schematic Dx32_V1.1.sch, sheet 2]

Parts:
B1: KMB24F; MBS; JLCPCB-PART C113927
B2, B3, B4, B5, B6, B7, B8, B9, B10, B11, B12, B13, B14, B15, B16, B17, B18, B19, B20, B21, B22, B23, B24, B25, B26, B27, B28, B29, B30, B31, B32: KMB24F; MBS
C11, C12, C13, C14, C15, C16, C17, C18, C19, C20, C21, C22, C23, C24, C25, C26, C27, C28, C29, C30, C31, C32, C33, C34, C35, C36, C37, C38, C39, C40, C41, C42: 100n; C0402
OK1: TLP290-4; MINI-FLAT-16; JLCPC-PART C39031
OK2, OK3, OK4, OK5, OK6, OK7, OK8: TLP290-4; MINI-FLAT-16
R9, R10, R11, R12, R13, R14, R15, R16, R17, R18, R19, R20, R21, R22, R23, R24, R25, R26, R27, R28, R29, R30, R31, R32, R33, R34, R35, R36, R37, R38, R39, R40: 33; R0402
RN1, RN2, RN3, RN4, RN5, RN6, RN7, RN8: 4R-N0603-ARV; 0603-ARV
T1: red; CHIP-LED0805; JLCPCB-PART C84256
T2, T3, T4, T5, T6, T7, T8, T9, T10, T11, T12, T13, T14, T15, T16, T17, T18, T19, T20, T21, T22, T23, T24, T25, T26, T27, T28, T29, T30, T31, T32: red; CHIP-LED0805
X1, X2, X3, X4: 180-10

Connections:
A0: OK1.10 (COL); also elsewhere on the board
A1: OK1.12 (COL); also elsewhere on the board
A2: OK1.14 (COL); also elsewhere on the board
A3: OK1.16 (COL); also elsewhere on the board
A4: T1.C; also elsewhere on the board
A5: T2.C; also elsewhere on the board
A6: T3.C; also elsewhere on the board
A7: T4.C; also elsewhere on the board
B6: T23.C; also elsewhere on the board
B7: T24.C; also elsewhere on the board
C0: T12.C; also elsewhere on the board
C1: T11.C; also elsewhere on the board
C2: T10.C; also elsewhere on the board
C3: T9.C; also elsewhere on the board
C4: OK3.10 (COL); also elsewhere on the board
C5: OK3.12 (COL); also elsewhere on the board
C6: OK3.14 (COL); also elsewhere on the board
C7: OK3.16 (COL); also elsewhere on the board
DCC1: B1.AC2, B2.AC2, B3.AC2, B4.AC2, C11.2, C12.2, C13.2, C14.2, OK1.2 (C), OK1.4 (C), OK1.6 (C), OK1.8 (C), X1.1
DCC2: B5.AC2, B6.AC2, B7.AC2, B8.AC2, C15.2, C16.2, C17.2, C18.2, OK2.2 (C), OK2.4 (C), OK2.6 (C), OK2.8 (C), X1.10
DCC3: B9.AC2, B10.AC2, B11.AC2, B12.AC2, C19.2, C20.2, C21.2, C22.2, OK3.2 (C), OK3.4 (C), OK3.6 (C), OK3.8 (C), X2.1
DCC4: B13.AC2, B14.AC2, B15.AC2, B16.AC2, C23.2, C24.2, C25.2, C26.2, OK4.2 (C), OK4.4 (C), OK4.6 (C), OK4.8 (C), X2.10
DCC5: B17.AC2, B18.AC2, B19.AC2, B20.AC2, C27.2, C28.2, C29.2, C30.2, OK5.2 (C), OK5.4 (C), OK5.6 (C), OK5.8 (C), X3.1
DCC6: B21.AC2, B22.AC2, B23.AC2, B24.AC2, C31.2, C32.2, C33.2, C34.2, OK6.2 (C), OK6.4 (C), OK6.6 (C), OK6.8 (C), X3.10
DCC7: B25.AC2, B26.AC2, B27.AC2, B28.AC2, C35.2, C36.2, C37.2, C38.2, OK7.2 (C), OK7.4 (C), OK7.6 (C), OK7.8 (C), X4.1
DCC8: B29.AC2, B30.AC2, B31.AC2, B32.AC2, C39.2, C40.2, C41.2, C42.2, OK8.2 (C), OK8.4 (C), OK8.6 (C), OK8.8 (C), X4.10
E2: T22.C; also elsewhere on the board
E3: T21.C; also elsewhere on the board
E4: OK6.10 (COL); also elsewhere on the board
E5: OK6.12 (COL); also elsewhere on the board
E6: OK6.14 (COL); also elsewhere on the board
E7: OK6.16 (COL); also elsewhere on the board
F0: T25.C; also elsewhere on the board
F1: T26.C; also elsewhere on the board
F2: T27.C; also elsewhere on the board
F3: T28.C; also elsewhere on the board
F4: OK7.16 (COL); also elsewhere on the board
F5: OK7.14 (COL); also elsewhere on the board
F6: OK7.12 (COL); also elsewhere on the board
F7: OK7.10 (COL); also elsewhere on the board
GND: OK1.9 (EMIT), OK1.11 (EMIT), OK1.13 (EMIT), OK1.15 (EMIT), OK2.9 (EMIT), OK2.11 (EMIT), OK2.13 (EMIT), OK2.15 (EMIT), OK3.9 (EMIT), OK3.11 (EMIT), OK3.13 (EMIT), OK3.15 (EMIT), OK4.9 (EMIT), OK4.11 (EMIT), OK4.13 (EMIT), OK4.15 (EMIT), OK5.9 (EMIT), OK5.11 (EMIT), OK5.13 (EMIT), OK5.15 (EMIT), OK6.9 (EMIT), OK6.11 (EMIT), OK6.13 (EMIT), OK6.15 (EMIT), OK7.9 (EMIT), OK7.11 (EMIT), OK7.13 (EMIT), OK7.15 (EMIT), OK8.9 (EMIT), OK8.11 (EMIT), OK8.13 (EMIT), OK8.15 (EMIT); also elsewhere on the board
H0: T20.C; also elsewhere on the board
H1: T19.C; also elsewhere on the board
H2: T18.C; also elsewhere on the board
H3: T17.C; also elsewhere on the board
H4: OK5.16 (COL); also elsewhere on the board
H5: OK5.14 (COL); also elsewhere on the board
H6: OK5.12 (COL); also elsewhere on the board
H7: OK5.10 (COL); also elsewhere on the board
J0: T8.C; also elsewhere on the board
J1: T7.C; also elsewhere on the board
J2: T6.C; also elsewhere on the board
J3: T5.C; also elsewhere on the board
J4: OK2.10 (COL); also elsewhere on the board
J5: OK2.12 (COL); also elsewhere on the board
J6: OK2.14 (COL); also elsewhere on the board
J7: OK2.16 (COL); also elsewhere on the board
K0: T29.C; also elsewhere on the board
K1: T30.C; also elsewhere on the board
K2: T31.C; also elsewhere on the board
K3: T32.C; also elsewhere on the board
K4: OK8.10 (COL); also elsewhere on the board
K5: OK8.12 (COL); also elsewhere on the board
K6: OK8.14 (COL); also elsewhere on the board
K7: OK8.16 (COL); also elsewhere on the board
L0: OK4.16 (COL); also elsewhere on the board
L1: OK4.14 (COL); also elsewhere on the board
L2: OK4.12 (COL); also elsewhere on the board
L3: OK4.10 (COL); also elsewhere on the board
L4: T16.C; also elsewhere on the board
L5: T15.C; also elsewhere on the board
L6: T14.C; also elsewhere on the board
L7: T13.C; also elsewhere on the board
unnamed: B1.+, B1.-
unnamed: B1.AC1, R9.2, X1.2
unnamed: B5.+, B5.-
unnamed: C11.1, OK1.7 (A), R9.1
unnamed: B2.+, B2.-
unnamed: B2.AC1, R10.2, X1.3
unnamed: B3.+, B3.-
unnamed: C12.1, OK1.5 (A), R10.1
unnamed: B24.AC1, R32.2, X3.9
unnamed: C13.1, OK1.3 (A), R11.1
unnamed: B4.+, B4.-
unnamed: B4.AC1, R12.2, X1.5
unnamed: C14.1, OK1.1 (A), R12.1
unnamed: B5.AC1, R13.2, X1.6
unnamed: C15.1, OK2.7 (A), R13.1
unnamed: B6.+, B6.-
unnamed: B6.AC1, R14.2, X1.7
unnamed: C16.1, OK2.5 (A), R14.1
unnamed: B7.+, B7.-
unnamed: B7.AC1, R15.2, X1.8
unnamed: C17.1, OK2.3 (A), R15.1
unnamed: B8.+, B8.-
unnamed: B8.AC1, R16.2, X1.9
unnamed: C18.1, OK2.1 (A), R16.1
unnamed: RN1.1, T1.A
unnamed: RN1.2 (1), T2.A
unnamed: RN1.3 (1), T3.A
unnamed: RN1.4 (1), T4.A
unnamed: RN2.1, T5.A
unnamed: RN2.2 (1), T6.A
unnamed: RN2.3 (1), T7.A
unnamed: RN2.4 (1), T8.A
unnamed: B9.+, B9.-
unnamed: B9.AC1, R17.2, X2.2
unnamed: C19.1, OK3.7 (A), R17.1
unnamed: B10.+, B10.-
unnamed: B10.AC1, R18.2, X2.3
unnamed: C20.1, OK3.5 (A), R18.1
unnamed: B11.+, B11.-
unnamed: B11.AC1, R19.2, X2.4
unnamed: C21.1, OK3.3 (A), R19.1
unnamed: B12.+, B12.-
unnamed: B12.AC1, R20.2, X2.5
unnamed: C22.1, OK3.1 (A), R20.1
unnamed: B13.+, B13.-
unnamed: B13.AC1, R21.2, X2.6
unnamed: C23.1, OK4.7 (A), R21.1
unnamed: B14.+, B14.-
unnamed: B14.AC1, R22.2, X2.7
unnamed: C24.1, OK4.5 (A), R22.1
unnamed: B15.+, B15.-
unnamed: B15.AC1, R23.2, X2.8
unnamed: C25.1, OK4.3 (A), R23.1
unnamed: B16.+, B16.-
unnamed: B16.AC1, R24.2, X2.9
unnamed: C26.1, OK4.1 (A), R24.1
unnamed: B17.+, B17.-
unnamed: B17.AC1, R25.2, X3.2
unnamed: C27.1, OK5.7 (A), R25.1
unnamed: B18.+, B18.-
unnamed: B18.AC1, R26.2, X3.3
unnamed: C28.1, OK5.5 (A), R26.1
unnamed: B19.+, B19.-
unnamed: B19.AC1, R27.2, X3.4
unnamed: C29.1, OK5.3 (A), R27.1
unnamed: B20.+, B20.-
unnamed: B20.AC1, R28.2, X3.5
unnamed: C30.1, OK5.1 (A), R28.1
unnamed: B21.+, B21.-
unnamed: C31.1, OK6.7 (A), R29.1
unnamed: B22.+, B22.-
unnamed: B32.AC1, R40.2, X4.9
unnamed: C32.1, OK6.5 (A), R30.1
unnamed: B23.+, B23.-
unnamed: B23.AC1, R31.2, X3.8
unnamed: C33.1, OK6.3 (A), R31.1
unnamed: B24.+, B24.-
unnamed: B31.AC1, R39.2, X4.8
unnamed: C34.1, OK6.1 (A), R32.1
unnamed: B25.+, B25.-
unnamed: B25.AC1, R33.2, X4.2
unnamed: C35.1, OK7.7 (A), R33.1
unnamed: B26.+, B26.-
unnamed: B26.AC1, R34.2, X4.3
unnamed: C36.1, OK7.5 (A), R34.1
unnamed: B27.+, B27.-
unnamed: B27.AC1, R35.2, X4.4
unnamed: B3.AC1, R11.2, X1.4
unnamed: C37.1, OK7.3 (A), R35.1
unnamed: B28.+, B28.-
unnamed: B28.AC1, R36.2, X4.5
unnamed: C38.1, OK7.1 (A), R36.1
unnamed: B29.+, B29.-
unnamed: C39.1, OK8.7 (A), R37.1
unnamed: B30.+, B30.-
unnamed: C40.1, OK8.5 (A), R38.1
unnamed: B31.+, B31.-
unnamed: B30.AC1, R38.2, X4.7
unnamed: C41.1, OK8.3 (A), R39.1
unnamed: B32.+, B32.-
unnamed: C42.1, OK8.1 (A), R40.1
unnamed: RN3.1, T9.A
unnamed: RN3.2 (1), T10.A
unnamed: RN3.3 (1), T11.A
unnamed: RN3.4 (1), T12.A
unnamed: RN4.1, T13.A
unnamed: RN4.2 (1), T14.A
unnamed: RN4.3 (1), T15.A
unnamed: RN4.4 (1), T16.A
unnamed: B22.AC1, R30.2, X3.7
unnamed: RN5.1, T17.A
unnamed: RN5.2 (1), T18.A
unnamed: RN5.3 (1), T19.A
unnamed: RN5.4 (1), T20.A
unnamed: RN6.1, T21.A
unnamed: RN6.2 (1), T22.A
unnamed: RN6.3 (1), T23.A
unnamed: RN6.4 (1), T24.A
unnamed: RN7.1, T25.A
unnamed: RN7.2 (1), T26.A
unnamed: RN7.3 (1), T27.A
unnamed: RN7.4 (1), T28.A
unnamed: RN8.1, T29.A
unnamed: RN8.2 (1), T30.A
unnamed: RN8.3 (1), T31.A
unnamed: RN8.4 (1), T32.A
unnamed: B21.AC1, R29.2, X3.6
unnamed: B29.AC1, R37.2, X4.6
VCC: RN1.5 (2), RN1.6 (2), RN1.7 (2), RN1.8 (2), RN2.5 (2), RN2.6 (2), RN2.7 (2), RN2.8 (2), RN3.5 (2), RN3.6 (2), RN3.7 (2), RN3.8 (2), RN4.5 (2), RN4.6 (2), RN4.7 (2), RN4.8 (2), RN5.5 (2), RN5.6 (2), RN5.7 (2), RN5.8 (2), RN6.5 (2), RN6.6 (2), RN6.7 (2), RN6.8 (2), RN7.5 (2), RN7.6 (2), RN7.7 (2), RN7.8 (2), RN8.5 (2), RN8.6 (2), RN8.7 (2), RN8.8 (2); also elsewhere on the board

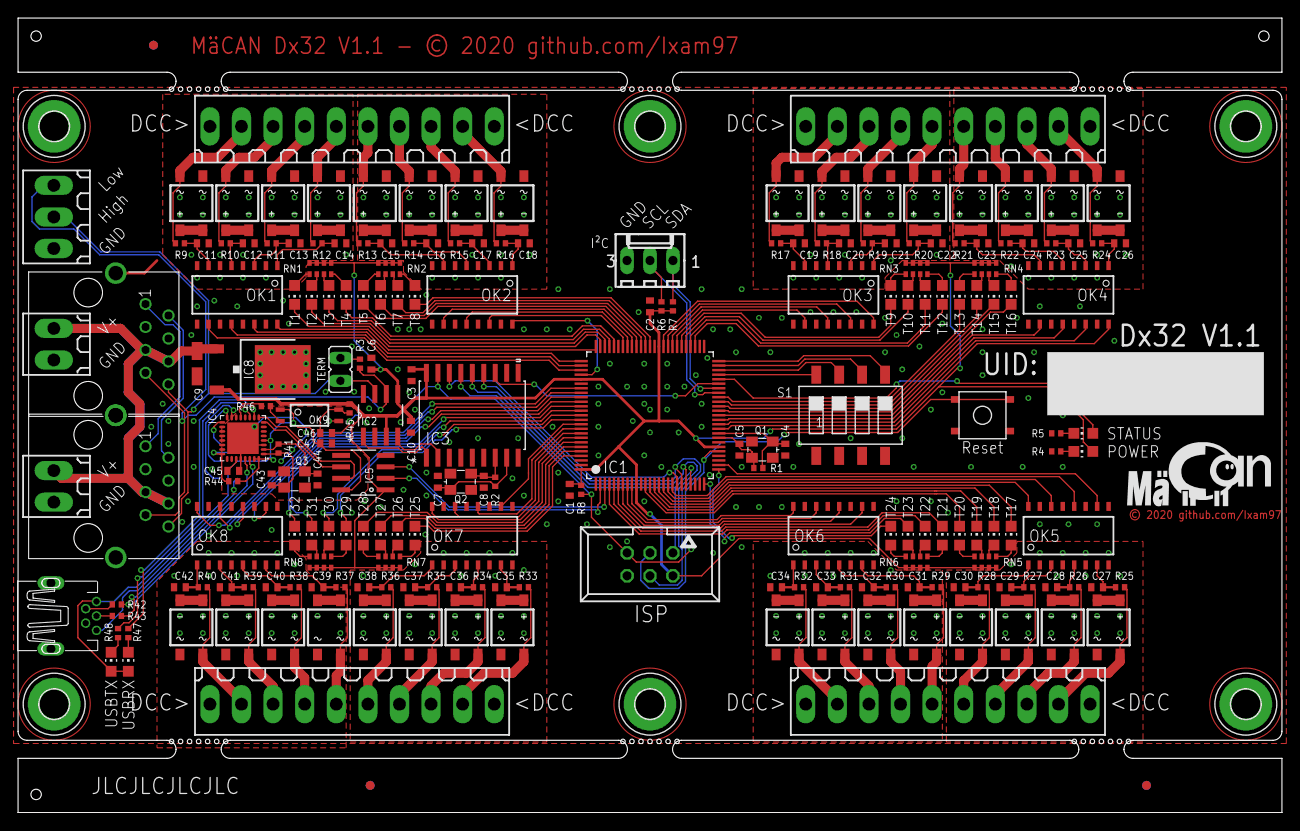
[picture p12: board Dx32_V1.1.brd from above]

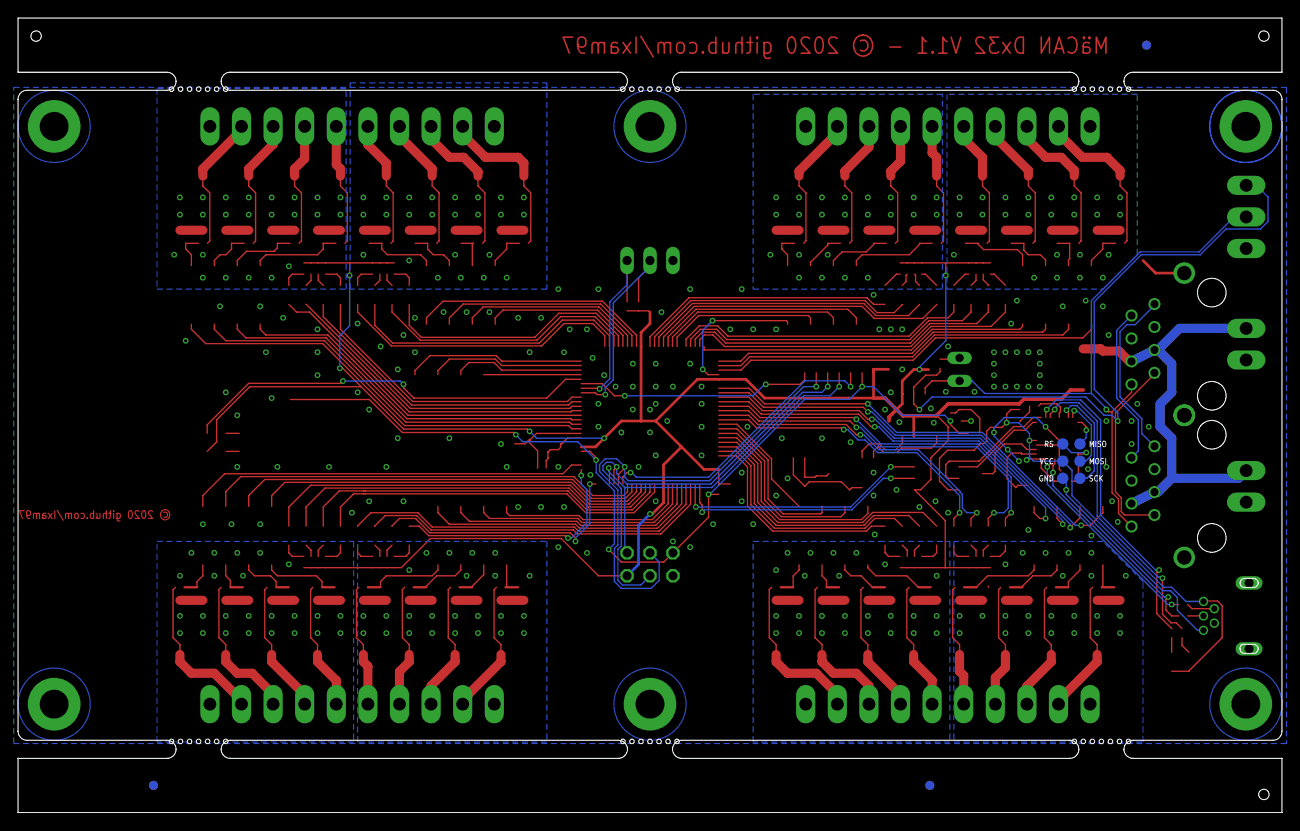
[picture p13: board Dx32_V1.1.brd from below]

Board: 2 copper layers, 140.0 x 88.0 mm, 229 parts (6 on the bottom side), 253 nets.

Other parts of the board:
U$2, U$3, U$5: JLCPCB_TOOLINGHOLE
U$6, U$7, U$8: FIDUCIAL
U$9, U$10, U$11, U$12, U$13, U$14: MOUSEBITESX7
U$17: LOGO_2

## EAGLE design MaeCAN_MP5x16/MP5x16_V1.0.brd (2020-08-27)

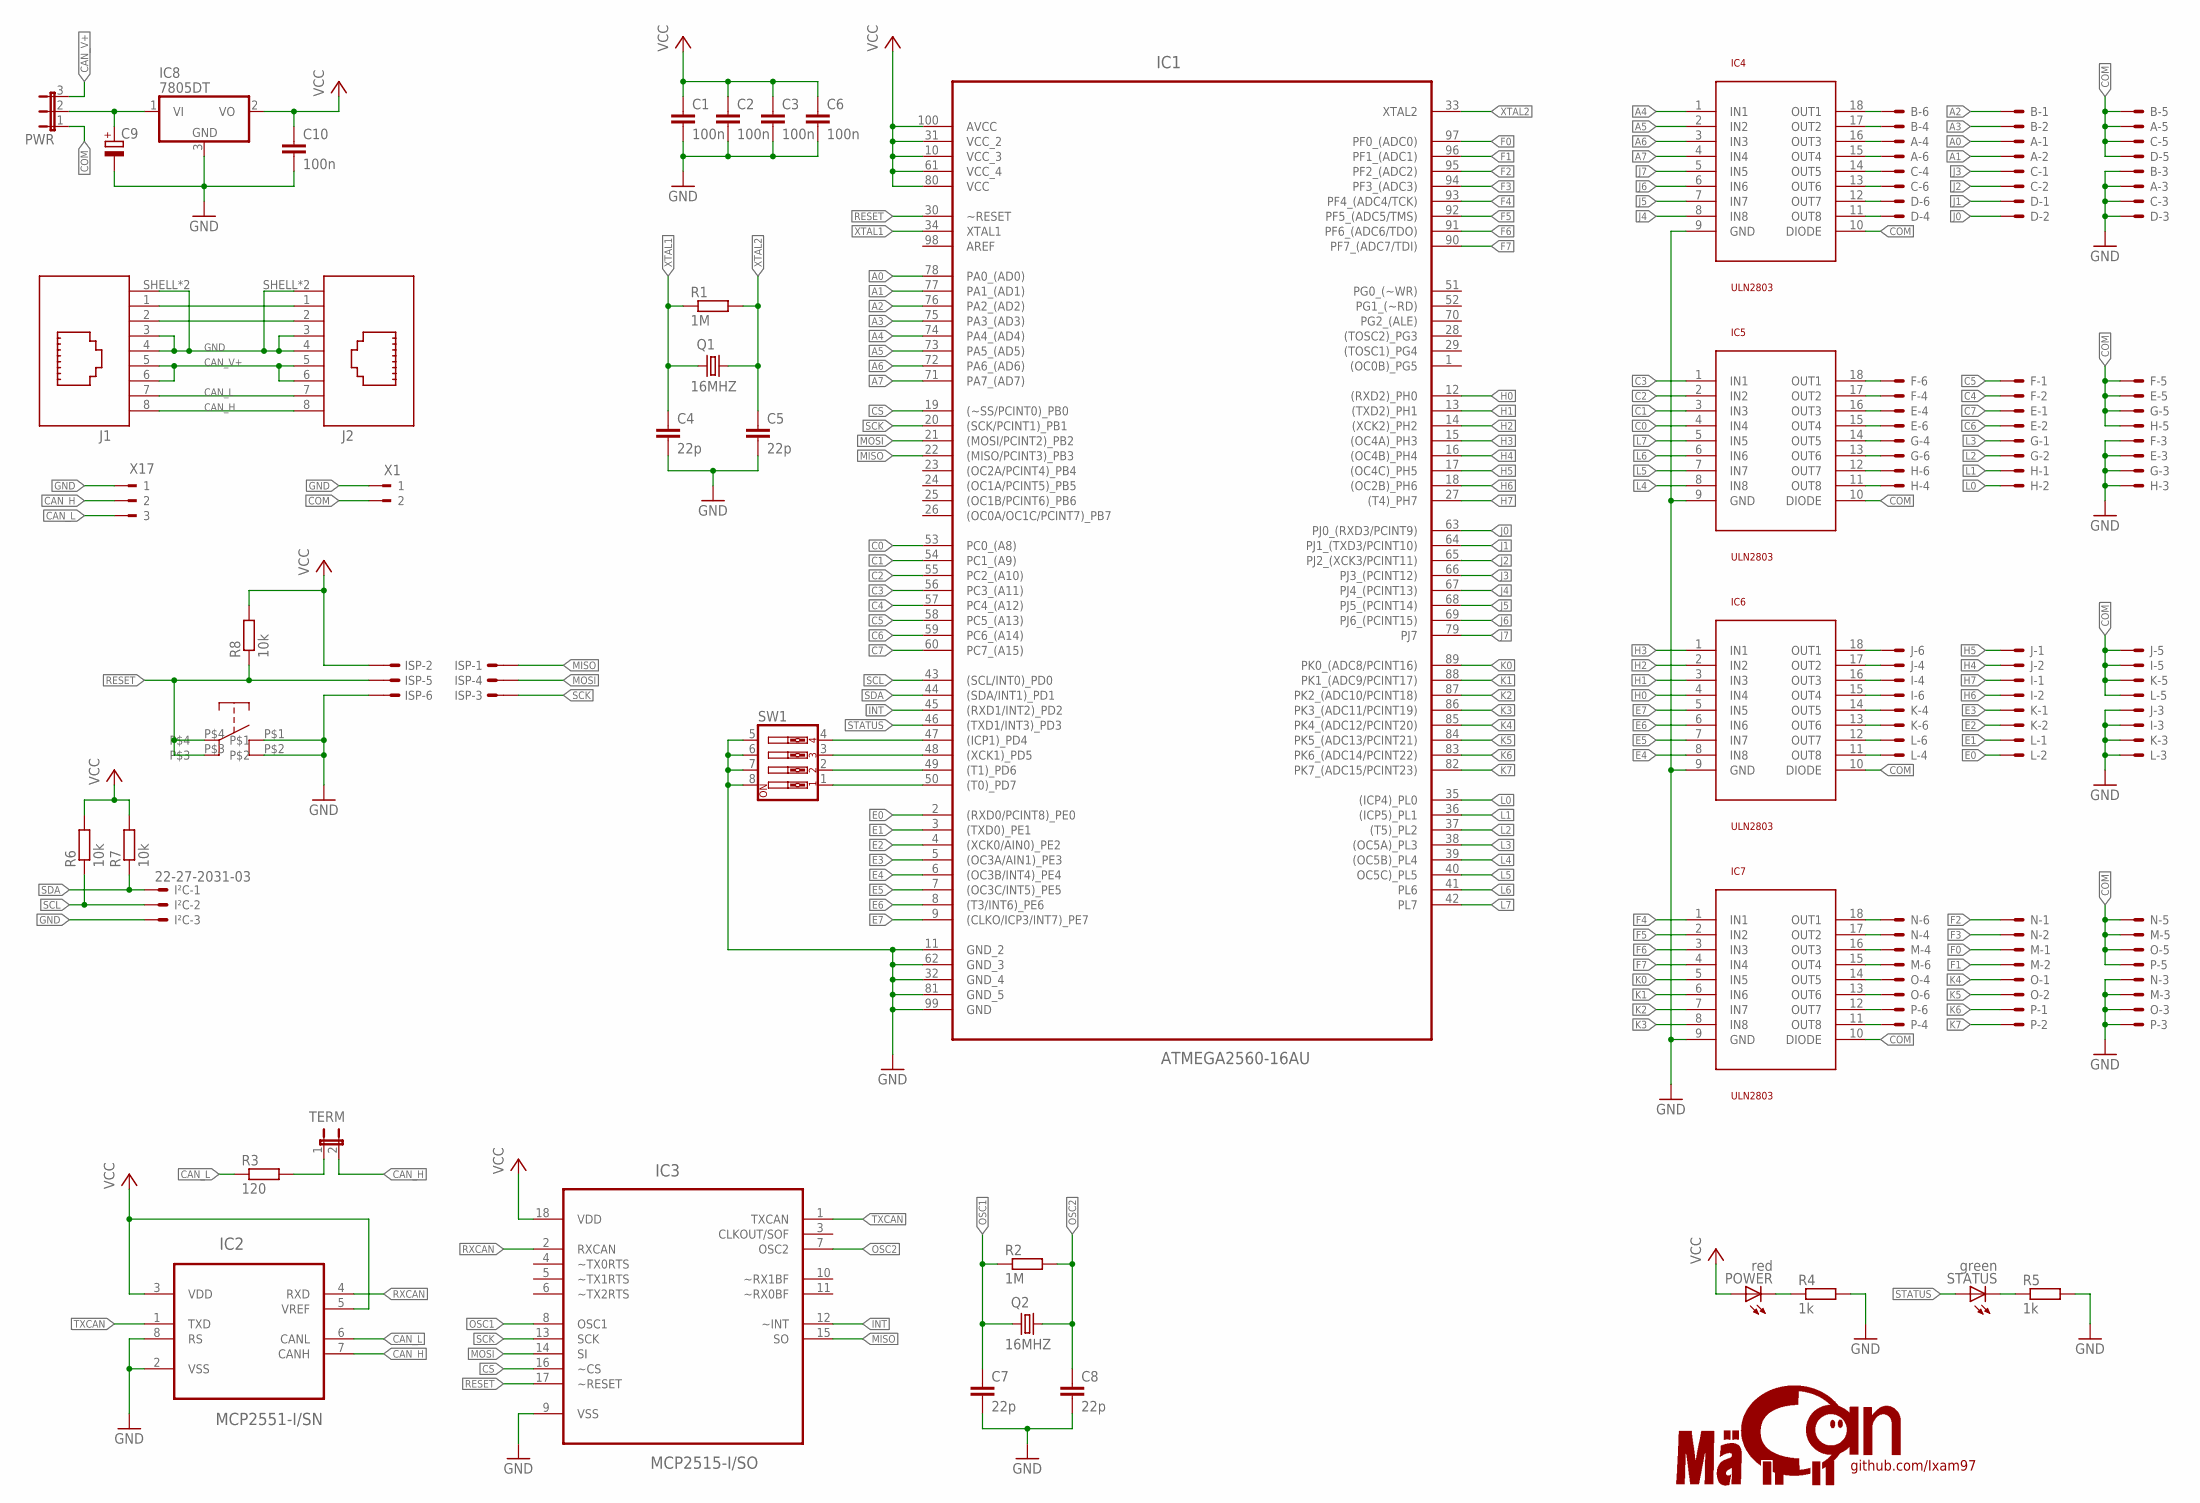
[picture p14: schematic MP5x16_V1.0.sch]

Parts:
A: 22-27-2061-06; 6410-06
B: 22-27-2061-06; 6410-06
C: 22-27-2061-06; 6410-06
C1, C2, C3, C6, C10: 100n; C0402
C4, C5, C7, C8: 22p; C0402
C9: CPOL-EUCT3216; CT3216
D: 22-27-2061-06; 6410-06
E: 22-27-2061-06; 6410-06
F: 22-27-2061-06; 6410-06
G: 22-27-2061-06; 6410-06
H: 22-27-2061-06; 6410-06
I: 22-27-2061-06; 6410-06
IC1: ATMEGA2560-16AU; QFP50P1600X1600X120-100N
IC2: MCP2551-I/SN; SOIC127P600X175-8N
IC3: MCP2515-I/SO; SOIC127P1034X264-18N
IC4, IC5, IC6, IC7: ULN2803; SO18L
IC8: 7805DT; TO252
ISP: 057-006-1
I²C: 22-27-2031-03; 6410-03
J: 22-27-2061-06; 6410-06
J1, J2: 615008140421
K: 22-27-2061-06; 6410-06
L: 22-27-2061-06; 6410-06
M: 22-27-2061-06; 6410-06
N: 22-27-2061-06; 6410-06
O: 22-27-2061-06; 6410-06
P: 22-27-2061-06; 6410-06
POWER: red; CHIP-LED0805
PWR: JP2E; JP2
Q1, Q2: 16MHZ; 3.2X2.5_KX-7
R1, R2: 1M; R0402
R3: 120; R0402
R4, R5: 1k; R0402
R6, R7, R8: 10k; R0402
STATUS: green; CHIP-LED0805
SW1: SW_DIP-4; EDG-04
TERM: JP1E; JP1
U$1: LOGO
U$15: BUTTON_JLC; BUTTON
X1: 180-2
X17: 180-3

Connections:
A0: A.1, IC1.78 (PA0_(AD0))
A1: A.2, IC1.77 (PA1_(AD1))
A2: B.1, IC1.76 (PA2_(AD2))
A3: B.2, IC1.75 (PA3_(AD3))
A4: IC1.74 (PA4_(AD4)), IC4.1 (IN1)
A5: IC1.73 (PA5_(AD5)), IC4.2 (IN2)
A6: IC1.72 (PA6_(AD6)), IC4.3 (IN3)
A7: IC1.71 (PA7_(AD7)), IC4.4 (IN4)
C0: IC1.53 (PC0_(A8)), IC5.4 (IN4)
C1: IC1.54 (PC1_(A9)), IC5.3 (IN3)
C2: IC1.55 (PC2_(A10)), IC5.2 (IN2)
C3: IC1.56 (PC3_(A11)), IC5.1 (IN1)
C4: F.2, IC1.57 (PC4_(A12))
C5: F.1, IC1.58 (PC5_(A13))
C6: E.2, IC1.59 (PC6_(A14))
C7: E.1, IC1.60 (PC7_(A15))
CAN_H: IC2.7 (CANH), J1.8, J2.8, TERM.2, X17.2
CAN_L: IC2.6 (CANL), J1.7, J2.7, R3.1, X17.3
CAN_V+: J1.5, J1.6, J2.5, J2.6, PWR.3
COM: A.5, B.5, C.5, D.5, E.5, F.5, G.5, H.5, I.5, IC4.10 (DIODE), IC5.10 (DIODE), IC6.10 (DIODE), IC7.10 (DIODE), J.5, K.5, L.5, M.5, N.5, O.5, P.5, PWR.1, X1.2
CS: IC1.19 ((~SS/PCINT0)_PB0), IC3.16 (~CS)
E0: IC1.2 ((RXD0/PCINT8)_PE0), L.2
E1: IC1.3 ((TXD0)_PE1), L.1
E2: IC1.4 ((XCK0/AIN0)_PE2), K.2
E3: IC1.5 ((OC3A/AIN1)_PE3), K.1
E4: IC1.6 ((OC3B/INT4)_PE4), IC6.8 (IN8)
E5: IC1.7 ((OC3C/INT5)_PE5), IC6.7 (IN7)
E6: IC1.8 ((T3/INT6)_PE6), IC6.6 (IN6)
E7: IC1.9 ((CLKO/ICP3/INT7)_PE7), IC6.5 (IN5)
F0: IC1.97 (PF0_(ADC0)), M.1
F1: IC1.96 (PF1_(ADC1)), M.2
F2: IC1.95 (PF2_(ADC2)), N.1
F3: IC1.94 (PF3_(ADC3)), N.2
F4: IC1.93 (PF4_(ADC4/TCK)), IC7.1 (IN1)
F5: IC1.92 (PF5_(ADC5/TMS)), IC7.2 (IN2)
F6: IC1.91 (PF6_(ADC6/TDO)), IC7.3 (IN3)
F7: IC1.90 (PF7_(ADC7/TDI)), IC7.4 (IN4)
GND: A.3, B.3, C.3, C1.2, C2.2, C3.2, C4.2, C5.2, C6.2, C7.2, C8.2, C9.-, C10.2, D.3, E.3, F.3, G.3, H.3, I.3, IC1.11 (GND_2), IC1.32 (GND_4), IC1.62 (GND_3), IC1.81 (GND_5), IC1.99 (GND), IC2.2 (VSS), IC2.8 (RS), IC3.9 (VSS), IC4.9 (GND), IC5.9 (GND), IC6.9 (GND), IC7.9 (GND), IC8.3 (GND), ISP.6, I²C.3, J.3, J1.3, J1.4, J1.SHELL (SHIELD), J1.SHELL1 (SHIELD), J2.3, J2.4, J2.SHELL (SHIELD), J2.SHELL1 (SHIELD), K.3, L.3, M.3, N.3, O.3, P.3, R4.2, R5.2, SW1.5, SW1.6, SW1.7, SW1.8, U$15.P$1, U$15.P$2, X1.1, X17.1
H0: IC1.12 ((RXD2)_PH0), IC6.4 (IN4)
H1: IC1.13 ((TXD2)_PH1), IC6.3 (IN3)
H2: IC1.14 ((XCK2)_PH2), IC6.2 (IN2)
H3: IC1.15 ((OC4A)_PH3), IC6.1 (IN1)
H4: IC1.16 ((OC4B)_PH4), J.2
H5: IC1.17 ((OC4C)_PH5), J.1
H6: I.2, IC1.18 ((OC2B)_PH6)
H7: I.1, IC1.27 ((T4)_PH7)
INT: IC1.45 ((RXD1/INT2)_PD2), IC3.12 (~INT)
J0: D.2, IC1.63 (PJ0_(RXD3/PCINT9))
J1: D.1, IC1.64 (PJ1_(TXD3/PCINT10))
J2: C.2, IC1.65 (PJ2_(XCK3/PCINT11))
J3: C.1, IC1.66 (PJ3_(PCINT12))
J4: IC1.67 (PJ4_(PCINT13)), IC4.8 (IN8)
J5: IC1.68 (PJ5_(PCINT14)), IC4.7 (IN7)
J6: IC1.69 (PJ6_(PCINT15)), IC4.6 (IN6)
J7: IC1.79 (PJ7), IC4.5 (IN5)
K0: IC1.89 (PK0_(ADC8/PCINT16)), IC7.5 (IN5)
K1: IC1.88 (PK1_(ADC9/PCINT17)), IC7.6 (IN6)
K2: IC1.87 (PK2_(ADC10/PCINT18)), IC7.7 (IN7)
K3: IC1.86 (PK3_(ADC11/PCINT19)), IC7.8 (IN8)
K4: IC1.85 (PK4_(ADC12/PCINT20)), O.1
K5: IC1.84 (PK5_(ADC13/PCINT21)), O.2
K6: IC1.83 (PK6_(ADC14/PCINT22)), P.1
K7: IC1.82 (PK7_(ADC15/PCINT23)), P.2
L0: H.2, IC1.35 ((ICP4)_PL0)
L1: H.1, IC1.36 ((ICP5)_PL1)
L2: G.2, IC1.37 ((T5)_PL2)
L3: G.1, IC1.38 ((OC5A)_PL3)
L4: IC1.39 ((OC5B)_PL4), IC5.8 (IN8)
L5: IC1.40 (OC5C)_PL5), IC5.7 (IN7)
L6: IC1.41 (PL6), IC5.6 (IN6)
L7: IC1.42 (PL7), IC5.5 (IN5)
MISO: IC1.22 ((MISO/PCINT3)_PB3), IC3.15 (SO), ISP.1
MOSI: IC1.21 ((MOSI/PCINT2)_PB2), IC3.14 (SI), ISP.4
unnamed: B.4, IC4.17 (OUT2)
unnamed: B.6, IC4.18 (OUT1)
unnamed: A.4, IC4.16 (OUT3)
unnamed: A.6, IC4.15 (OUT4)
unnamed: C.4, IC4.14 (OUT5)
unnamed: C.6, IC4.13 (OUT6)
unnamed: D.6, IC4.12 (OUT7)
unnamed: D.4, IC4.11 (OUT8)
unnamed: F.6, IC5.18 (OUT1)
unnamed: F.4, IC5.17 (OUT2)
unnamed: E.6, IC5.15 (OUT4)
unnamed: E.4, IC5.16 (OUT3)
unnamed: G.4, IC5.14 (OUT5)
unnamed: G.6, IC5.13 (OUT6)
unnamed: H.6, IC5.12 (OUT7)
unnamed: H.4, IC5.11 (OUT8)
unnamed: IC1.47 ((ICP1)_PD4), SW1.4
unnamed: IC1.48 ((XCK1)_PD5), SW1.3
unnamed: IC1.49 ((T1)_PD6), SW1.2
unnamed: IC1.50 ((T0)_PD7), SW1.1
unnamed: J1.1, J2.1
unnamed: IC6.12 (OUT7), L.6
unnamed: IC7.12 (OUT7), P.6
unnamed: IC6.11 (OUT8), L.4
unnamed: I.4, IC6.16 (OUT3)
unnamed: I.6, IC6.15 (OUT4)
unnamed: IC6.14 (OUT5), K.4
unnamed: IC6.13 (OUT6), K.6
unnamed: IC6.17 (OUT2), J.4
unnamed: IC6.18 (OUT1), J.6
unnamed: IC7.11 (OUT8), P.4
unnamed: IC7.17 (OUT2), N.4
unnamed: IC7.16 (OUT3), M.4
unnamed: IC7.15 (OUT4), M.6
unnamed: IC7.14 (OUT5), O.4
unnamed: IC7.13 (OUT6), O.6
unnamed: IC7.18 (OUT1), N.6
unnamed: J1.2, J2.2
unnamed: POWER.C, R4.1
unnamed: R3.2, TERM.1
unnamed: R5.1, STATUS.C
OSC1: C7.1, IC3.8 (OSC1), Q2.1, R2.1
OSC2: C8.1, IC3.7 (OSC2), Q2.3 (2), R2.2
RESET: IC1.30 (~RESET), IC3.17 (~RESET), ISP.5, R8.1, U$15.P$3, U$15.P$4
RXCAN: IC2.4 (RXD), IC3.2 (RXCAN)
SCK: IC1.20 ((SCK/PCINT1)_PB1), IC3.13 (SCK), ISP.3
SCL: IC1.43 ((SCL/INT0)_PD0), I²C.2, R6.1
SDA: IC1.44 ((SDA/INT1)_PD1), I²C.1, R7.1
STATUS: IC1.46 ((TXD1/INT3)_PD3), STATUS.A
TXCAN: IC2.1 (TXD), IC3.1 (TXCAN)
V+: C9.+, IC8.1 (VI), PWR.2
VCC: C1.1, C2.1, C3.1, C6.1, C10.1, IC1.10 (VCC_3), IC1.31 (VCC_2), IC1.61 (VCC_4), IC1.80 (VCC), IC1.100 (AVCC), IC2.3 (VDD), IC2.5 (VREF), IC3.18 (VDD), IC8.2 (VO), ISP.2, POWER.A, R6.2, R7.2, R8.2
XTAL1: C4.1, IC1.34 (XTAL1), Q1.1, R1.1
XTAL2: C5.1, IC1.33 (XTAL2), Q1.3 (2), R1.2

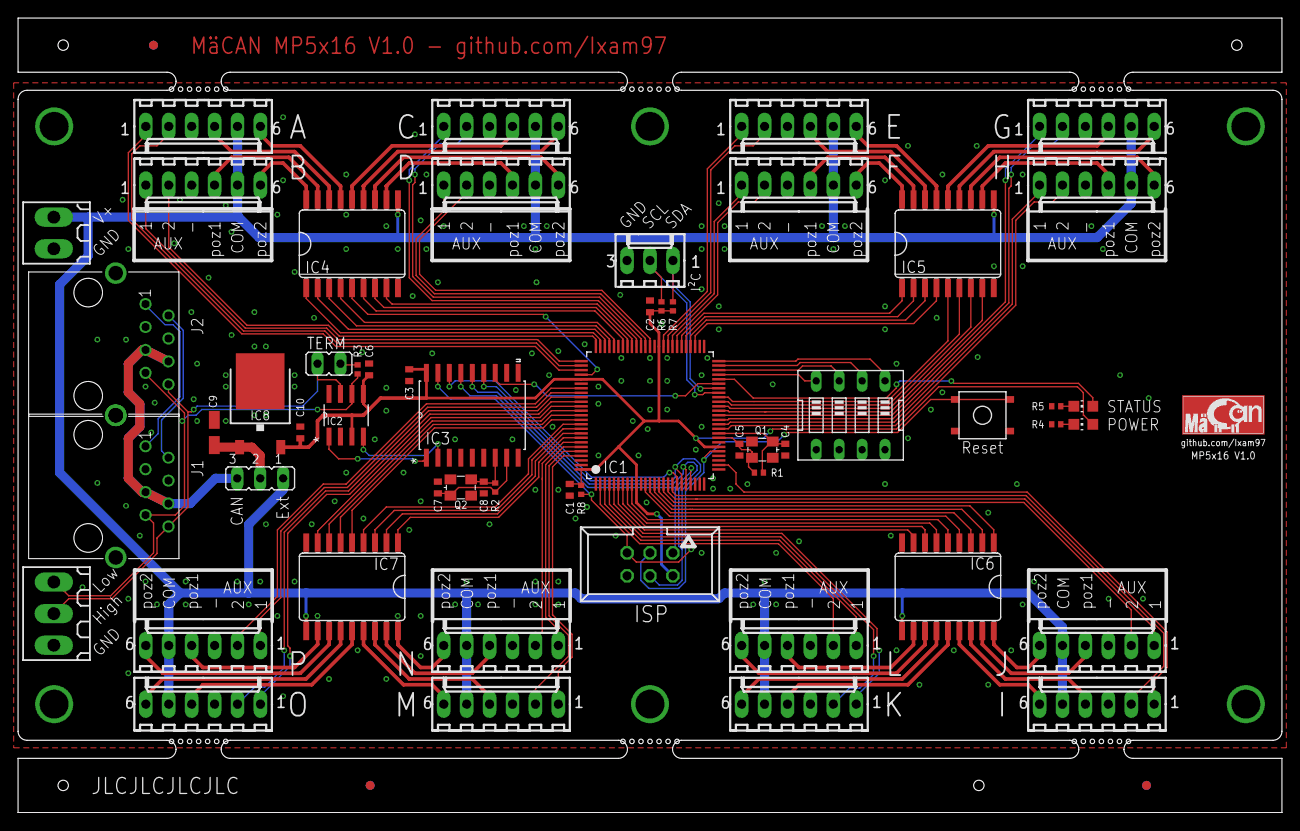
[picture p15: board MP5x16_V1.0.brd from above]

Board: 2 copper layers, 140.0 x 88.0 mm, 70 parts (0 on the bottom side), 127 nets.

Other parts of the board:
U$2, U$3, U$4, U$5: JLCPCB_TOOLINGHOLE
U$6, U$7, U$8: FIDUCIAL
U$9, U$10, U$11, U$12, U$13, U$14: MOUSEBITESX7

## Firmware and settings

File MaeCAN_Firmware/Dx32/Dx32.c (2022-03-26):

/*
 * ----------------------------------------------------------------------------
 * "THE BEER-WARE LICENSE" (Revision 42):
 * Maximilian Goldschmidt wrote this file. As long as you retain this notice you
 * can do whatever you want with this stuff. If we meet some day, and you think
 * this stuff is worth it, you can buy me a beer in return.
 * 
 * ----------------------------------------------------------------------------
 * https://github.com/Ixam97
 * ----------------------------------------------------------------------------
 * MaeCAN Dx32
 * V 1.1
 * [2022-03-26.1]
 */

/* 
 * ----------------------------------------------------------------------------
 * EEPROM ADDRESS MAP
 * ----------------------------------------------------------------------------
 * 0x03ff : Bootloader request flag
 * 0x0000 : LED brightness
 * 0x0002 : Number of used inputs
 * 0x0004 : Number of sense inputs
 * 0x0006 : Bus ID
 * 0x0008 : Start address of first input
 */
#define EEPROM_LED_BRIGHTNESS	0x0000
#define EEPROM_NUM_INPUTS		0x0002
#define EEPROM_NUM_SENSE		0x0004
#define EEPROM_BUS_ID			0x0006
#define EEPROM_START_ADR		0x0008
#define EEPROM_BOOTLOADER_FLAG	0x03ff

// Maximum values for config chanels
#define MAX_LED_BRIGHTNESS		0xff
#define MAX_NUM_INPUTS			32
#define MAX_NUM_SENSE			4
#define MAX_BUS_ID				0xffff
#define MAX_START_ADR			0xffff

#define NAME "M\u00E4CAN 32-fach Gleisbelegtmelder"
#define BASE_UID 0x4D430000
#define ITEM "Dx32"
#define VERSION 0x0101
#define TYPE 0x0053

#include <stdlib.h>
#include <avr/io.h>
#include <avr/boot.h>
#include <avr/eeprom.h>
#include <util/delay.h>
#include <avr/interrupt.h>
#include <avr/wdt.h>
#include <avr/pgmspace.h>
#include <string.h>

#include "../Common/mcan.h"
#include "Dx32v1.0_Pindefs.h"

const uint8_t ledLookupTable[] PROGMEM = {
	  0,  0,  0,  0,  0,  0,  0,  0,  0,  0,  0,  0,  1,  1,  1,  1,
	  1,  1,  1,  1,  2,  2,  2,  2,  2,  2,  3,  3,  3,  3,  4,  4,
	  4,  4,  5,  5,  5,  5,  6,  6,  6,  7,  7,  7,  8,  8,  8,  9,
	  9,  9, 10, 10, 11, 11, 11, 12, 12, 13, 13, 14, 14, 15, 15, 16,
	 16, 17, 17, 18, 18, 19, 19, 20, 20, 21, 21, 22, 23, 23, 24, 24,
	 25, 26, 26, 27, 28, 28, 29, 30, 30, 31, 32, 32, 33, 34, 35, 35,
	 36, 37, 38, 38, 39, 40, 41, 42, 42, 43, 44, 45, 46, 47, 47, 48,
	 49, 50, 51, 52, 53, 54, 55, 56, 56, 57, 58, 59, 60, 61, 62, 63,
	 64, 65, 66, 67, 68, 69, 70, 71, 73, 74, 75, 76, 77, 78, 79, 80,
	 81, 82, 84, 85, 86, 87, 88, 89, 91, 92, 93, 94, 95, 97, 98, 99,
	100,102,103,104,105,107,108,109,111,112,113,115,116,117,119,120,
	121,123,124,126,127,128,130,131,133,134,136,137,139,140,142,143,
	145,146,148,149,151,152,154,155,157,158,160,162,163,165,166,168,
	170,171,173,175,176,178,180,181,183,185,186,188,190,192,193,195,
	197,199,200,202,204,206,207,209,211,213,215,217,218,220,222,224,
	226,228,230,232,233,235,237,239,241,243,245,247,249,251,253,255
	};

canFrame frame_in;

uint16_t serial_nbr;
uint16_t id;

uint8_t silent;							// Ignore ping requests

uint8_t reset_request;					// 1 if software reset is requested, else 0

uint32_t heartbeat_millis;				// Time counter for status LED
uint32_t last_heartbeat_millis;

//char uart_to_can_buffer[25];
//uint8_t uart_to_can_buffer_index;

uint8_t t_led_brightness;
uint8_t t_led_brightness_set;

uint8_t num_inputs;		// Number of used inputs

uint16_t bus_id;		// ID of the S88 Bus

uint16_t start_adr;		// Address of the first input

uint8_t s_led_state;
uint8_t s_led_brightness = 0;
uint8_t s_led_brightness_set = 0;
uint8_t s_led_rising = 1;

uint8_t duty_cycle_counter;
uint8_t last_duty_cycle_counter;
uint8_t new_duty_cycle;

uint8_t trk_state_actual[4];							// actual electric occupation state
uint8_t trk_state_logic[4] = {0xff, 0xff, 0xff, 0xff};	// logic occupation state
uint8_t trk_state_last[4];								// last logic occupation state
uint16_t trk_timeout[4][8];								// timeout counters
uint8_t trk_timeout_flag[4];							// timeout counter flags, high bit means count up
uint16_t trk_timeout_millis = 1500;						// timeout time in milliseconds
uint8_t trk_sense_flag = 0xff;							// high bit indicates missing track power, one bit per four ports
uint8_t trk_sense_mask[4];								// masking ports to be handled as sense port (no timeout, change when power is off)
uint8_t trk_sense_ports;								// number of sense ports (0,1,2,4,8)
const uint8_t trk_sense_ports_table[] PROGMEM = {0,1,2,4,8};
const uint8_t trk_sense_reverse_table[] PROGMEM = {0,1,2,0,3,0,0,0,4};
uint8_t trk_LEDs[4];									// LED state to be set
uint8_t trk_blinker;									// blink value provider
uint16_t trk_blinker_millis;							// blink counter

uint8_t current_input;
uint8_t last_input;


//
// Status LED blinking pattern.
// Heartbeat blinking during normal operation.
//
void heartbeat() {
	
	if (heartbeat_millis >= 1200) {
		//setLow(statusPin);
		s_led_rising = 0;
		heartbeat_millis = 0;
	} else if (heartbeat_millis >= 1000) {
		//setHigh(statusPin);
		s_led_rising = 1;
	} else if (heartbeat_millis >= 800) {
		//setLow(statusPin);
		s_led_rising = 0;
	} else if (heartbeat_millis >= 600) {
		//setHigh(statusPin);
		s_led_rising = 1;
	}
	
	if (trk_blinker_millis >= 500) {
		trk_blinker = 0;
		trk_blinker_millis = 0;
	} else if (trk_blinker_millis >= 250) {
		trk_blinker = 1;
	}
	
	if (heartbeat_millis != last_heartbeat_millis) {
		last_heartbeat_millis = heartbeat_millis;
		
		for (uint8_t i = 0; i < 4; i++) {
			for (uint8_t j = 0; j < 8; j++) {
				// Track occupation timeout
				trk_timeout[i][j] += (trk_timeout_flag[i] >> j) & 0b1;
			}
		}
		
		if (s_led_rising == 1 && s_led_brightness_set <= (0xff - 3)) {
			s_led_brightness_set += 3;
			s_led_brightness = (uint8_t) pgm_read_byte (&ledLookupTable[s_led_brightness_set]);
		} else if (s_led_rising == 0 && s_led_brightness_set >= 3) {
			s_led_brightness_set -= 3;
			s_led_brightness = (uint8_t) pgm_read_byte (&ledLookupTable[s_led_brightness_set]);
		}
		
	}	
	
}

//
// Update sense flags and masks.
//
void applySenseFlagsMasks(void) {
	switch (trk_sense_ports) {
		case 8: {
			trk_sense_flag = (TRKA & 0b00000001) + ((TRKA >> 6) & 0b00000010) + ((TRKB << 2) & 0b00000100) + ((TRKB >> 4) & 0b00001000) + ((TRKC << 4) & 0b00010000) + ((TRKC >> 2) & 0b00100000) + ((TRKD << 6) & 0b01000000) + (TRKD & 0b10000000);
			trk_sense_mask[0] = 0b10000001;
			trk_sense_mask[1] = 0b10000001;
			trk_sense_mask[2] = 0b10000001;
			trk_sense_mask[3] = 0b10000001;
			break;
		}
		case 4: {
			trk_sense_flag = (TRKA & 0b00000001) + ((TRKA << 1) & 0b00000010) + ((TRKB << 2) & 0b00000100) + ((TRKB << 3) & 0b00001000) + ((TRKC << 4) & 0b00010000) + ((TRKC << 5) & 0b00100000) + ((TRKD << 6) & 0b01000000) + ((TRKD << 7) & 0b10000000);
			trk_sense_mask[0] = 0b00000001;
			trk_sense_mask[1] = 0b00000001;
			trk_sense_mask[2] = 0b00000001;
			trk_sense_mask[3] = 0b00000001;
			break;
		}
		case 2: {
			trk_sense_flag = (TRKA & 0b00000001) + ((TRKA << 1) & 0b00000010) + ((TRKA << 2) & 0b00000100) + ((TRKA << 3) & 0b00001000) + ((TRKC << 4) & 0b00010000) + ((TRKC << 5) & 0b00100000) + ((TRKC << 6) & 0b01000000) + ((TRKC << 7) & 0b10000000);
			trk_sense_mask[0] = 0b00000001;
			trk_sense_mask[1] = 0b00000000;
			trk_sense_mask[2] = 0b00000001;
			trk_sense_mask[3] = 0b00000000;
			break;
		}
		case 1: {
			trk_sense_flag = (TRKA & 0b00000001) + ((TRKA << 1) & 0b00000010) + ((TRKA << 2) & 0b00000100) + ((TRKA << 3) & 0b00001000) + ((TRKA << 4) & 0b00010000) + ((TRKA << 5) & 0b00100000) + ((TRKA << 6) & 0b01000000) + ((TRKA << 7) & 0b10000000);
			trk_sense_mask[0] = 0b00000001;
			trk_sense_mask[1] = 0b00000000;
			trk_sense_mask[2] = 0b00000000;
			trk_sense_mask[3] = 0b00000000;
			break;
		}
		default: {
			trk_sense_flag = 0;
			trk_sense_mask[0] = 0b00000000;
			trk_sense_mask[1] = 0b00000000;
			trk_sense_mask[2] = 0b00000000;
			trk_sense_mask[3] = 0b00000000;
			break;
		}
	}
}

//
// Updates for config values.
// Returns 1 on success, 0 when value too large.
//
uint8_t updateLEDBrightness(uint16_t _value) {
	if (_value <= MAX_LED_BRIGHTNESS) {
		t_led_brightness_set = _value;
		t_led_brightness = (uint8_t) pgm_read_byte (&ledLookupTable[t_led_brightness_set]);
		eeprom_update_word((void*)EEPROM_LED_BRIGHTNESS, t_led_brightness_set);
		return 1;
	}
	return 0;
}

uint8_t updateNumInputs(uint16_t _value) {
	if (_value <= MAX_NUM_INPUTS) {
		num_inputs = _value;
		eeprom_update_word((void *)EEPROM_NUM_INPUTS, num_inputs);
		return 1;
	}
	return 0;
}

uint8_t updateSensePorts(uint16_t _value) {
	if (_value <= MAX_NUM_SENSE) {
		trk_sense_ports = (uint8_t)pgm_read_byte(&trk_sense_ports_table[_value]);
		eeprom_update_word((void*)EEPROM_NUM_SENSE, trk_sense_ports);
		return 1;
	}
	return 0;
}

uint8_t updateBusID(uint16_t _value) {
	if (_value <= MAX_BUS_ID) {
		bus_id = _value;
		eeprom_update_word((void*)EEPROM_BUS_ID, bus_id);
		return 1;
	}
	return 0;
}

uint8_t updateStartAdr(uint16_t _value) {
	if (_value <= MAX_START_ADR) {
		start_adr = _value;
		eeprom_update_word((void *)EEPROM_START_ADR, start_adr);
		return 1;
	}
	return 0;
}

//
// Report Inputs when requested.
//
void reportInput(uint16_t _s88_bus_id, uint16_t _s88_port_id) {
	if (_s88_port_id >= start_adr && _s88_port_id < start_adr + num_inputs && _s88_bus_id == bus_id) {
		uint8_t index = _s88_port_id - start_adr;
		sendS88Event(((uint32_t)_s88_bus_id << 16) + _s88_port_id, (trk_state_logic[index / 8] >> (index % 8)) & 0b1, (trk_state_last[index / 8] >> (index % 8)) & 0b1);
	}
}

void reportAllInputs(void) {
	for (uint8_t i = 0; i < num_inputs; i++) {
		sendS88Event(((uint32_t)bus_id << 16) + i + start_adr, (trk_state_logic[i / 8] >> (i % 8)) & 0b1, (trk_state_last[i / 8] >> (i % 8)) & 0b1);
	}
}

//
// Fun with Frames.
//
void handleCanFramePointer(canFrame *frame_in) {
	
	switch (frame_in->cmd) {
		
		case 0x40 : {
			// Bootloader request
			// THIS SECTION IS REQUIRED FOR THE BOOTLOADER TO WORK DURING NORMAL OPARATION
			
			if (frame_in->resp == 0 && frame_in->dlc == 4) {
				if (compareUID(frame_in->data, mcan_uid) == 1) {
					
					// Write bootloader request flag to EEPROM and reset.
					eeprom_update_byte((void *)EEPROM_BOOTLOADER_FLAG, 1);
					_delay_ms(100);
					reset_request = 1;
				}
			}
			break;
		}
		case CMD_PING : {
			// Ping
			if (frame_in->resp == 0 && silent == 0) sendPingFrame(VERSION, TYPE);
			break;
		}
		case CMD_S88_EVENT : {
			// S88 querry
			if (frame_in->resp == 0 && frame_in->dlc == 0) {
				reportAllInputs();
			} else if (frame_in->resp == 0 && frame_in->dlc == 2) {
				if (((uint16_t)frame_in->data[0] << 8) + ((uint16_t)frame_in->data[1]) == bus_id) reportAllInputs();
			} else if (frame_in->resp == 0 && frame_in->dlc == 4) {
				reportInput(((uint16_t)frame_in->data[0] << 8) + ((uint16_t)frame_in->data[1]), ((uint16_t)frame_in->data[2] << 8) + ((uint16_t)frame_in->data[3]));
			}
			break;
		}
		case CMD_CONFIG : {
			// Config data
			if (frame_in->resp == 0 && compareUID(frame_in->data, mcan_uid) == 1 && silent == 0) {
				switch (frame_in->data[4]) {
					case 0 :
					sendDeviceInfo(id, 0, 5, ITEM, NAME);
					break;
					case 1 :
					sendConfigInfoSlider(1, 0, 0xff, t_led_brightness_set, "Melder-Helligkeit_0_255");
					break;
					case 2 :
					sendConfigInfoSlider(2, 1, 32, num_inputs, "Verwendete Eing\u00E4nge_1_32");
					break;
					case 3 :
					sendConfigInfoDropdown(3, 5, (uint8_t)pgm_read_byte(&trk_sense_reverse_table[trk_sense_ports]), "Anzahl Sense-Eing\u00E4nge_0_1_2_4_8");
					break;
					case 4:
					sendConfigInfoSlider(4, 0, 0xffff, 0, "Buskennung_0_65535");
					break;
					case 5:
					sendConfigInfoSlider(5, 1, 0xffff, 1, "Startadresse_1_65535");
					break;
					default : {
						break;
					}
				}
			}
			break;
		}
		
		case SYS_CMD : {
			// Write config value
			if (frame_in->resp == 0 && compareUID(frame_in->data, mcan_uid) == 1 && frame_in->data[4] == SYS_STAT && frame_in->dlc == 8) {
				uint16_t value = ((uint16_t)frame_in->data[6] << 8) + (uint16_t)frame_in->data[7];
				
				switch (frame_in->data[5]) {
					case 1: // LED Brightness
					sendConfigConfirm(1, updateLEDBrightness(value));
					break;
					case 2: // Number of inputs
					sendConfigConfirm(2, updateNumInputs(value));
					break;
					case 3: // Number of sense ports
					sendConfigConfirm(3, updateSensePorts(value));
					break;
					case 4: // Bus ID
					sendConfigConfirm(4, updateBusID(value));
					break;
					case 5: // Start address
					sendConfigConfirm(5, updateStartAdr(value));
					break;
					default:
					sendConfigConfirm(frame_in->data[5], 0);
					break;
					
				}
				
			// Send config value
			} else if (frame_in->resp == 0 && compareUID(frame_in->data, mcan_uid) == 1 && frame_in->data[4] == SYS_STAT && frame_in->dlc == 6) {
				
				switch (frame_in->data[5]) {
					case 1: // LED Brightness
					sendStatus(1, t_led_brightness_set);
					break;
					case 2: // Number of inputs
					sendStatus(2, num_inputs);
					break;
					case 3: // Number of sense ports
					sendStatus(3, (uint8_t)pgm_read_byte(&trk_sense_reverse_table[trk_sense_ports]));
					break;
					case 4: // Bus ID
					sendStatus(4, bus_id);
					break;
					case 5: // Start address
					sendStatus(5, start_adr);
					break;
					default:
					break;
					
				}
			}
		}
		default : break;
	}
}

//
// Update logic states of track occupation.
//
void updateOccupationLogic(void) {
	for (uint8_t i = 0; i < 4; i++) {
		for (uint8_t j = 0; j < 8; j++) {
			
			// Get bit values for specific port
			uint8_t trk_bit_actual = (trk_state_actual[i] >> j) & 0b1;
			uint8_t trk_bit_logic = (trk_state_logic[i] >> j) & 0b1;
			uint8_t trk_bit_sense = (~trk_sense_flag >> ((i * 2) + (j / 4))) & 0b1;
			uint8_t trk_bit_sense_mask = (trk_sense_mask[i] >> j) & 0b1;
			
			
			if (trk_bit_actual < trk_bit_logic && (8 * i + j) < num_inputs) {
				// Don't do logic changes when input not used
				// Change logic state on occupation
				trk_state_logic[i] &= ~(1 << j);
				trk_state_last[i] |= (1 << j);
				sendS88Event(((uint32_t)bus_id << 16) + (8 * i + j) + start_adr, (~trk_bit_logic & 0b1), (~trk_bit_actual & 0b1));
				} else if (trk_bit_actual == 0) {
				// Reset timeout when occupation returns
				trk_timeout_flag[i] &= ~(1 << j);
				trk_timeout[i][j] = 0;
				} else if (trk_bit_logic < trk_bit_actual && (trk_timeout[i][j] >= trk_timeout_millis || trk_bit_sense_mask == 1)) {
				// Wait for timeout before resetting occupation
				trk_state_logic[i] |= (1 << j);
				trk_state_last[i] &= ~(1 << j);
				sendS88Event(((uint32_t)bus_id << 16) + (8 * i + j) + start_adr, (~trk_bit_logic & 0b1), (~trk_bit_actual & 0b1));
				trk_timeout_flag[i] &= ~(1 << j);
				trk_timeout[i][j] = 0;
				} else if (trk_bit_logic < trk_bit_actual && trk_timeout[i][j] == 0 && ((trk_bit_sense == 1) || (trk_bit_sense_mask == 1))) {
				// start timeout
				trk_timeout_flag[i] |= (1 << j);
				} else if (trk_bit_sense == 0 && trk_timeout[i][j] > 0) {
				// Reset timeout when no track power
				trk_timeout_flag[i] &= ~(1 << j);
				trk_timeout[i][j] = 0;
			}
			
			if (trk_bit_sense == 0 && (8 * i + j) < num_inputs) {
				// Blink LEDs if no track power sensed
				trk_LEDs[i] = (trk_LEDs[i] & ~(1 << j)) + ((~(~(trk_bit_logic & 0b1) & trk_blinker) & 0b1) << j);
			} else if (trk_LEDs[i] != trk_state_logic[i] && (8 * i + j) < num_inputs) {
				trk_LEDs[i] = (trk_LEDs[i] & ~(1 << j)) + (trk_bit_logic << j);
			} else if ((8 * i + j) >= num_inputs) {
				// turn on LEDs permanently when input unused
				trk_LEDs[i] = (trk_LEDs[i] & ~(1 << j));
			}
		}
	}
}

//
// main
//
int main(void)
{
	/************************************************************************/
	/*  INIT                                                                */
	/************************************************************************/
	
	// Read config values from EEPROM
	t_led_brightness_set = (uint8_t)eeprom_read_word((void *)EEPROM_LED_BRIGHTNESS);
	t_led_brightness = (uint8_t) pgm_read_byte (&ledLookupTable[t_led_brightness_set]);
	num_inputs = (uint8_t)eeprom_read_word((void *)EEPROM_NUM_INPUTS);
	trk_sense_ports = (uint8_t)eeprom_read_word((void *)EEPROM_NUM_SENSE);
	bus_id = eeprom_read_word((void*)EEPROM_BUS_ID);
	start_adr = eeprom_read_word((void *)EEPROM_START_ADR);
	
	
	initPins();
	
	// Get serial number and calculate UID and hash
	serial_nbr = (uint16_t)(boot_signature_byte_get(22) << 8) | boot_signature_byte_get(23);
	id = serial_nbr;
	//uid = BASE_UID + serial_nbr;
	//hash = generateHash(uid);
	
	cli();	
	
	// Setup heartbeat timer:
	TCCR0A |= (1 << WGM01);					// Timer 0 clear time on compare match
	OCR0A = (F_CPU / (64 * 1000UL)) - 1;	// Timer 0 compare value
	TIMSK0 |= (1 << OCIE0A);				// Timer interrupt
	TCCR0B |= ((1 << CS01)|(1 << CS00));	// Set timer 0 prescaler to 64
	
	// Setup dimm timer:
	TCCR1A |= (1 << WGM11);					// Timer 1 clear time on compare match
	OCR1A = (F_CPU / (1 * 128000UL)) - 1;	// Timer 1 compare value (128kHz)
	TIMSK1 |= (1 << OCIE1A);				// Timer interrupt
	TCCR1B |= (1 << CS10);					// No prescaler
	sei();
	
	// Init CAN bus
	mcan_init(BASE_UID + serial_nbr);
	
	/************************************************************************/
	/* MAIN LOOP                                                            */
	/************************************************************************/
	
    while (1) 
    {
		// Read dip switch states
		if (readPin(dip_switch[0]) == 0) reset_request = 1; // Bootloader mode
		
		if (readPin(dip_switch[1]) == 0) use_nl = 1;		// Send [NL] after every SLCAN frame on UART
		else use_nl = 0;
		
		if (readPin(dip_switch[2]) == 0) silent = 1;		// Silent mode
		else silent = 0;
		
		heartbeat();	
		
		// Reading actual Track Values:
		readTracks();
		trk_state_actual[0] = TRKA;
		trk_state_actual[1] = TRKB;
		trk_state_actual[2] = TRKC;
		trk_state_actual[3] = TRKD;
		
		
		// Update sense flags and masks
		applySenseFlagsMasks();
		
		// Update logic occupation states
		updateOccupationLogic();
		
		// update LED registers depending on logic states
		LEDA = ~trk_LEDs[0];
		LEDB = ~trk_LEDs[1];
		LEDC = ~trk_LEDs[2];
		LEDD = ~trk_LEDs[3];
		
		// Handle new CAN frame
		if (readCanFrame(&frame_in) == 1) handleCanFramePointer(&frame_in);

		// Software reset.
		if (reset_request == 1) {
			
			reset_request = 0;
			cli();
			resetLEDs();
			wdt_enable(WDTO_15MS);
			while(1);
		}
    }
}


/************************************************************************/
/*  INTERRUPT SERVICE ROUTINES                                          */
/************************************************************************/

ISR(TIMER0_COMPA_vect) {
	// Count up time counters.
	heartbeat_millis++;
	trk_blinker_millis++;
	
}

ISR(TIMER1_COMPA_vect) {
	// Duty cycle counter.
	
	if (duty_cycle_counter == 0xff) {
		duty_cycle_counter = 0;
	} else {
		++duty_cycle_counter;
	}
	if (duty_cycle_counter < t_led_brightness && new_duty_cycle == 1) {
		// turn on all t_leds specified in LEDx-Byte at the beginning of a duty cycle
		new_duty_cycle = 0;
		setLEDs();
	} else if (duty_cycle_counter >= t_led_brightness && new_duty_cycle == 0) {
		// turn off all t_leds at end of brightness-cycle
		new_duty_cycle = 1;
		resetLEDs();
	}
	
	if (duty_cycle_counter < s_led_brightness && s_led_state == 0) {
		setHigh(statusPin);
		s_led_state = 1;
	} else if (duty_cycle_counter >= s_led_brightness  && s_led_state == 1) {
		setLow(statusPin);
		s_led_state = 0;
	}
	
}

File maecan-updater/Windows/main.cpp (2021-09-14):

/*
* ----------------------------------------------------------------------------
* "THE BEER-WARE LICENSE" (Revision 42):
* Maximilian Goldschmidt wrote this file. As long as you retain this notice you
* can do whatever you want with this stuff. If we meet some day, and you think
* this stuff is worth it, you can buy me a beer in return.
* 
* ----------------------------------------------------------------------------
* MäCAN-Updater
* ----------------------------------------------------------------------------
*
* This updater was made for the MäCAN-Bootloader only: https://github.com/Ixam97/MaeCAN-Bootloader/
*
* Last changed: [2021-09-14.1]
*/

#include <winsock2.h>
#include <windows.h>
#include <stdio.h>
#include <stdint.h>
#include <stdlib.h>
#include <string>
#include <getopt.h>
#include <iostream>
#include <fstream>

#define VERSION "1.0"
#define PAGE_SIZE 256

using namespace std;

extern char *optarg;

uint8_t complete_buffer[0xfffff];
uint32_t complete_buffer_index;

char IP[17] = "192.168.0.5";
int PORT = 15731;

uint32_t can_uid = 0;

uint8_t page_buffer[PAGE_SIZE];
uint8_t page_buffer_index = 0;
uint16_t page_count = 0;
uint8_t page_index = 0;

uint8_t remote_type = 0;
uint16_t remote_pagesize = 0;
uint16_t remote_pagecount = 0;

ifstream hexfile;

int checkForArguments(char *_optarg);
int printUsage();
int startWinsock(void);
int recvTimeOutTCP(SOCKET _s, long _sec, long _usec);
int sendCanFrame(SOCKET _s, uint8_t cmd, uint8_t dlc, uint8_t _data[8]);
int sendCanFrame(SOCKET _s, uint8_t cmd, uint8_t dlc, uint8_t _data[8], uint16_t _hash);
void sendPage(SOCKET _s, uint8_t page);

int main(int argc, char *argv[])
{
    printf("maecan-updater version %s\n", VERSION);
    char filepath[256];
    int opt;

    while ((opt = getopt(argc, argv, "f:t:i:p:?h")) != -1){
        switch (opt) {
        case '?':
        case 'h':
            return printUsage();
            break;
        case 'f':
            // File path
            if (checkForArguments(optarg)) return printUsage();
            strncpy(filepath, optarg, sizeof(filepath) - 1);
            break;
        case 't':
            // File path
            if (checkForArguments(optarg)) return printUsage();
            can_uid = stoul(optarg, NULL, 16);
            break;
        case 'i':
            // Remote IP address
            if (checkForArguments(optarg)) return printUsage();
            strncpy(IP, optarg, sizeof(IP) - 1);
            break;
        case 'p':
            // Remote port
            if (checkForArguments(optarg)) return printUsage();
            PORT = stoul(optarg, NULL, 10);
            break;
        default:
            return printUsage();
            break;
        }
    }

    if (argc <= 1) return printUsage();
    if (can_uid == 0) return printUsage();

    hexfile.open(filepath);

    if (!hexfile.is_open()) {
        printf("ERROR: Invalid file or path!\n");
        return 1;
    }
    char ch, s_byte_count[3], s_data_address[5], s_line_type[3], s_data_byte[3], s_extended_segment_address[5], s_address_offset[5], s_checksum[3];
    uint8_t byte_count, line_type, data_byte;
    uint16_t data_address, extended_segment_address;
    uint32_t address_offset = 0;

    //memset(complete_buffer, 0xff, 0xfffff);
    //memset(page_buffer, 0xff, PAGE_SIZE);
    memset(s_byte_count, 0, 3);
    memset(s_data_address, 0, 5);
    memset(s_address_offset, 0, 5);
    memset(s_extended_segment_address, 0, 5);
    memset(s_line_type, 0, 3);
    memset(s_data_byte, 0, 3);
    memset(s_checksum, 0, 3);

    uint16_t line_counter = 0;

    while (hexfile.get(ch)) {
        if (ch == ':') {
            line_counter++;
            // New line
            uint32_t checksum = 0;

            hexfile.get(s_byte_count[0]);
            hexfile.get(s_byte_count[1]);
            byte_count = stoul(s_byte_count, NULL, 16);
            //printf("Byte Count: %2d, ", byte_count);
            checksum += byte_count;

            hexfile.get(s_data_address[0]);
            hexfile.get(s_data_address[1]);
            hexfile.get(s_data_address[2]);
            hexfile.get(s_data_address[3]);
            data_address = stoul(s_data_address, NULL, 16);
            //printf("Address: 0x%04x, ", data_address);
            checksum += ((uint8_t)(data_address >> 8) + (uint8_t)data_address);

            hexfile.get(s_line_type[0]);
            hexfile.get(s_line_type[1]);
            line_type = stoul(s_line_type, NULL, 16);
            //printf("Record Type: 0x%02x ", line_type);
            checksum += line_type;

            if (line_type == 0x00) {
                // Program data
                //printf("Data: ");
                for (uint8_t i = 0; i < byte_count; i++) {
                    // Read data bytes to buffer
                    hexfile.get(s_data_byte[0]);
                    hexfile.get(s_data_byte[1]);
                    data_byte = stoul(s_data_byte, NULL, 16);
                    //printf("%02x ", data_byte);
                    checksum += data_byte;

                    complete_buffer[address_offset + data_address + i] = data_byte;
                    complete_buffer_index = address_offset + data_address + i;
                }

            } else if (line_type == 0x02) {
                // Extended Segment Address
                hexfile.get(s_extended_segment_address[0]);
                hexfile.get(s_extended_segment_address[1]);
                hexfile.get(s_extended_segment_address[2]);
                hexfile.get(s_extended_segment_address[3]);
                extended_segment_address = stoul(s_extended_segment_address, NULL, 16);
                checksum += ((uint8_t)(extended_segment_address >> 8) + (uint8_t)extended_segment_address);

                address_offset = extended_segment_address << 4;

            } else if (line_type == 0x04) {
                // Extended Linear Address
                hexfile.get(s_address_offset[0]);
                hexfile.get(s_address_offset[1]);
                hexfile.get(s_address_offset[2]);
                hexfile.get(s_address_offset[3]);
                address_offset = stoul(s_address_offset, NULL, 16);
                checksum += ((uint8_t)(address_offset >> 8) + (uint8_t)address_offset);

            }

            hexfile.get(s_checksum[0]);
            hexfile.get(s_checksum[1]);
            //printf("Checksum: 0x%02x ", (uint8_t)(-checksum));
            if ((uint8_t)(-checksum) == stoul(s_checksum, NULL, 16)) {
                //printf("Correct \n");
            } else {
                printf("\nERROR: Checksum does not match in line %d!\n", line_counter);
                return 1;
            }
        }
    }
    hexfile.close();

    printf("\nHex file parsing successfull.\n");

    // CAN communication:

    long rc;
    SOCKET s;
    SOCKADDR_IN addr;

    addr.sin_port = htons(PORT);
    addr.sin_family = AF_INET;
    addr.sin_addr.s_addr = inet_addr(IP);
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

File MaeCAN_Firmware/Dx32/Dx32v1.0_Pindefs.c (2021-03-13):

/*
 * ----------------------------------------------------------------------------
 * "THE BEER-WARE LICENSE" (Revision 42):
 * Maximilian Goldschmidt wrote this file. As long as you retain this notice you
 * can do whatever you want with this stuff. If we meet some day, and you think
 * this stuff is worth it, you can buy me a beer in return.
 * 
 * ----------------------------------------------------------------------------
 * https://github.com/Ixam97
 * ----------------------------------------------------------------------------
 * MaeCAN Dx32
 * V 1.1
 * [2021-03-13.1]
 */

#include "Dx32v1.0_Pindefs.h"

const uint8_t reverse_lookup[] PROGMEM = {0x0, 0x8, 0x4, 0xc, 0x2, 0xa, 0x6, 0xe, 0x1, 0x9, 0x5, 0xd, 0x3, 0xb, 0x7, 0xf};

void setOutput(ioPin _pin) {
	*_pin.ddr |= (1 << _pin.pin);
}

void setInput(ioPin _pin) {
	*_pin.ddr &= ~(1 << _pin.pin);
}

void setHigh(ioPin _pin) {
	*_pin.port |= (1 << _pin.pin);
}

void setLow(ioPin _pin) {
	*_pin.port &= ~(1 << _pin.pin);
}

uint8_t readPin(ioPin _pin) {
	if(*_pin.in & (1 << _pin.pin)) {
		return 1;
	} else {
		return 0;
	}
}

uint8_t reverseNibble(uint8_t _nibble) {
	return (uint8_t)pgm_read_byte(&reverse_lookup[_nibble & 0b00001111]);
}

uint8_t reverseByte(uint8_t _byte) {
	return ((uint8_t)pgm_read_byte(&reverse_lookup[_byte & 0b00001111]) << 4) | (uint8_t)pgm_read_byte(&reverse_lookup[_byte >> 4]);
}

void initPins() {
	
	statusPin.port = &PORTD;
	statusPin.ddr = &DDRD;
	statusPin.pin = 3;
	
	for (uint8_t i = 0; i < 4; i++) {
		dip_switch[i].port = &PORTD;
		dip_switch[i].ddr = &DDRD;
		dip_switch[i].in = &PIND;
		dip_switch[i].pin = 4 + i;
		setHigh(dip_switch[i]);
		setInput(dip_switch[i]);
	}
	
	
	setOutput(statusPin);
	
	PORTA = 0b11111111; // T1 - T8
	PORTJ = 0b11111111;
	
	DDRA = 0b11110000;
	DDRJ = 0b00001111;
	
	PORTC = 0b11111111; // T9 - T16
	PORTL = 0b11111111;
	
	DDRC = 0b00001111;
	DDRL = 0b11110000;
	
	PORTH = 0b11111111; // T17 - T24
	PORTE |= (0b11111100);
	PORTB |= (0b11000000);
	
	DDRH = 0b00001111;
	DDRE |= 0b00001100;
	DDRB |= 0b11000000;
	DDRE &= ~0b11110000;
	
	PORTF = 0b11111111; // T25 - T32
	PORTK = 0b11111111;
	
	DDRF = 0b00001111;
	DDRK = 0b00001111;
}

void readTracks(void) {
	
	TRKA = ((PINA & 0b00001111) + (PINJ & 0b11110000));
	TRKB = ((PINC >> 4) + (reverseNibble(PINL) << 4));
	TRKC = (reverseNibble(PINH >> 4) + (PINE & 0b11110000));
	TRKD = (reverseNibble(PINF >> 4) + (PINK & 0b11110000));
}

void setLEDs(void) {
	
	// T1 - T8
	PORTA &= ~(0b11110000 & (LEDA << 4));
	PORTJ &= ~(0b00001111 & reverseNibble(LEDA >> 4));
	
	// T9 - T16
	PORTC &= ~(0b00001111 & reverseNibble(LEDB));
	PORTL &= ~(0b11110000 & (reverseNibble(LEDB >> 4) << 4));
	
	PORTH &= ~(0b00001111 & reverseNibble(LEDC));
	PORTE &= ~(0b00001100 & reverseNibble(LEDC >> 4));
	PORTB &= ~(0b11000000 & LEDC);
	
	PORTF &= ~(0b00001111 & LEDD);
	PORTK &= ~(0b00001111 & (LEDD >> 4));
	
}

void resetLEDs(void) {
	PORTA |= 0b11110000;
	PORTJ |= 0b00001111;
	PORTC |= 0b00001111;
	PORTL |= 0b11110000;
	PORTH |= 0b00001111;
	PORTE |= 0b00001100;
	PORTB |= 0b11000000;
	PORTF |= 0b00001111;
	PORTK |= 0b00001111;
}

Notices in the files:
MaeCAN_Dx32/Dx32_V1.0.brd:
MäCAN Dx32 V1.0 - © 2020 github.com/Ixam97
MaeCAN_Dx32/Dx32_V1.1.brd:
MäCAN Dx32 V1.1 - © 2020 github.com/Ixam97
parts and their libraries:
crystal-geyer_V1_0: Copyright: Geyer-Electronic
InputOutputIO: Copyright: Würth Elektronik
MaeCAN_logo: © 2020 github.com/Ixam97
